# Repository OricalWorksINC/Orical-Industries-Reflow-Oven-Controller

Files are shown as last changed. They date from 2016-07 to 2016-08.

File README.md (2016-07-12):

Reflow Oven Controller
====================
Big Thanks to Ed Simmons <ed@estechnical.co.uk> , Karl Pitrich <karl@pitrich.com>
For all there hard work on the original code that this is based on.

**News**
New method of prosscesing for better performance!
Adding Serial for co-processor to process the steppers and other calculations and operations

 NEW HARDWARE COMING SOON AND FIRMWARE REVISIONS FOR TUNNLE OVENS!

**Arduino-based reflow oven controller with:**
* [PID] loop control
* [Wave Packet] and [Phase Fired] control for AC outputs
* graphic TFT LC-Display, drawing the temperature curves
  * using an [Adafruit 1.8" TFT] or derivate display
* solely controlled using a cheap rotary encoder and its single button
* stores up to 30 temperature profiles in EEPROM
* configurable PID-parameters
* simple, small hardware to drive loads up to 600V and up to 8A
* hardware can
  * measure two temperatures independently
  * drive two AC loads, such as heater and fan
* could also be used for slow coockers
* *Please Note*: Requires Arduino IDE 1.5.x or newer

(c) 2016 John Reichard <john@hobbywizards.com>
in part based on a project (c) 2013 Ed Simmons <ed@estechnical.co.uk> , (c) 2014 Karl Pitrich <karl@pitrich.com>

**Post action shot**

CycleWithOverflow | Warning
------------ | -------------

## Warning: This project operates with possibly lethal mains voltage. If you are unsure what to do, don't do it and get help from an experienced tinkerer with professional training.

**Completed build**

Completed1 | Completed2
------------ | -------------

Introduction
====================

This Reflow Oven Controller relies on an [Arduino Pro Micro], which is similar to the Leonardo and easily obtainable on eb*y for less than $10, plus my custom shield, which is actually more like a motherboard.

As I believe it is not wise to have a mess of wiring and tiny breakout-boards for operating mains powered equipment, I've decided to design custom board with easily obtainable components.

The hardware can be found in the [folder hardware], including the Eagle schematics and PCB layout files. It should fit the freemium version of Eagle. Here are preview images:

PCB
Schematic

From my manufacturing run, I have some spare PCBs and parts. They are available at my [tindie store].

The board contains the [Arduino Pro Micro], very simple [Zero crossing] detection circuit, used to align control logic to mains frequency, two [MAX31855] thermocouple-to-digital converters and two [Sharp S202S01] PCB-mount solid state relays, mounted on cheap [Fischer SK409 50,8] heat sinks. The current software uses only one of the thermocouples, so you need to populate one IC only. If you're lucky, you can get free samples of the MAX31855 from Maxim.

The software uses [PID] control of the heater and fan output for improved temperature stability. The heater AC load is controlled using [Wave Packet] control in order to minimize RF interference and load on the relay. For the fan motor, [Phase Fired] control has been implemented.

Please note that all important timings are *based on the mains frequency*, so the circuit will **not work** properly without mains connection.

But for testing, I've added an additional timer to simulate the zero-crossings, in order to run the software without being connected to mains. The software should work in 50 and 60Hz mains, the 60Hz version is not tested, though.

Errata and construction infos
========

Issue | Notes
------------ | -------------

Code can only be uploded with the Arduino 1.0.6 IDE or the LCD won't dysplay anything in my case.

Screenshots and usage information
========

Image | Information
------------ | -------------
CycleWithOverflow | *Display after a cylcle has been completed. The blue line is the setpoint, the red line the actual temperature measured by the thermocouple. Note that the graph wraps around automatically. 'Sp' is the current setpoint calculated by the PID loop. In the lower line there are: Current heater and fan outputs, both in percent, and the current temperature rise or drop rate in °C per second. The graph will draw orientation lines every 50°C up to the peak temperature set in the selected profile.*
MenuDefault | *The main menu can be navigated by rotating the encoder (sic!). Clicking enters the menu item, or navigates to the submenu. Doubleclick moves up or back or exits the menu item.*
FanSpeedEdit | *To edit a setting, click once to enter edit mode (red cursor), then rotate to change the value, click again to save. Doubleclick will exit without saving.*
MenuEditProfile | -
ProfileSettings | *Typical solder profile settings...*
ProfileSettingsEdit | *These parameters can be easily edited using the encoder as described above.*
MenuLoadProfile | *Up to 30 Profiles can be loaded and saved. You have to do this manually, so that you can have 'save-as' functionality without overwriting existing profiles.*
PIDValues | *Current pid values for my 1300W 20$ toaster oven.*
PIDValuesEdit | *Editing is simple, like above. Note that, unlike with the profile settings, the PID values will be automatically stored to EEPROM when you exit the submenu by doubleclicking.*

Obtaining the source code
====================

Get the code using `git`.

	git clone https://github.com/OricalWorksINC/reflowOvenController

or [download a Snapshot].

I've added some libraries I've used as submodules to the git repositroy, so it is important that, after cloning this repository, you do 

    git submodule update --init

to fetch all involved libraries. (See: [Submodule Cheat Sheet])

Installation
====================

Of course, you need to have the Arduino IDE installed. I've worked with version 1.5.x only and I will not support older versions. Get it from the [Arduino Download] page or upgrade you current Arduino setup.

There as several dependencies you need to install. 

If you are unfamiliar with Arduino Libraries, please read [the library guide].
Basically, each library needs to be liked or copied into your Arduino library folder.

On a Mac, this is how you link the submodule libraries to your Arduino libraries folder:

    cd ~/Documents/Arduino/Libraries
    ln -s ~/Development/<reflow source code>/libraries
    
My code uses [TimerOne] for basic timing, for the 1.8" TFT I've used [Adafruit_ST7735], which requires [Adafruit_GFX]. I **strongly suggest** to use my **modified version** of [Adafruit_ST7735-pit], as it **performs much better**, but requires you to use SPI, which my board does anyway.

For the user interface you require my own [Menu] and [ClickEncoder] libraries, which are included as submodules.

All other libraries need to be downloaded and installed.

After you've installed all libraries, open the Arduino IDE, open the ReflowController.pde sketch (using File->Open).

Select the right hardware from the Tools->Board menu. (Use Leonardo for the Pro Micro)

Compile the firmware (Sketch->Verify) to test everything is installed correctly. If something's wrong, feel free to post an issue here on github, I will look into it.

Now, choose the correct serial port from Tools->Serial Port and then upload the code.
*Remember* that a standard compile will get stuck at "Calibrating..." without proper mains connection, so that zero crossing interrupts can occur.

I could not fit PID Autotuning into the limited space of the Arduino in addition the normal code. So if you want to try to autotune you PID Loop, install the [PID_AutoTune] Library, `#define PIDTUNE 1` in the .ino file, then recompile and download do the Arduino.

As all timing relies on Zero Crossing detection, you need to `#define FAKE_HW 1` and install [TimerThree] when you want to run without actual hardware *and/or* without mains connection.

Things to note
====================

* The [MAX31855] does not like the thermocouple being grounded; It must be isolated from ground or earth.
* The PID Loop must be tuned individually for each oven. It will *not* work out of the box. 
* [PID Autotune] is not very useful, as it seems to be able to tune only to keep a specific temperature value, which is not what we do in a reflow oven. Also, at least my oven seems to be very non-linear when heating up.
* When rewiring inside your oven, use only wiring that can withstand high temperatures. I use silicone coated lace.
* Do not solder wiring inside you oven, the temperature might desolder you joints. **Crimp everything.**
* Use proper earth ground connection for your ovens chassis.
* 

 ******** How To Upgrade Arduino For Faster Speeds! *********
 
 To boost your Arduino Uno's performance up to 25% faster, all you have to do is replace the 16 MHz crystal with 20 MHz crystal, and update the bootloader with one that designed for this upgraded speed (see instruction below).
 
 Please note that this is NOT overclocking, we'll just tuning it to maximum speed allowed by manufacturer as stated in ATmega328 datasheet. So it's 100% safe and guaranteed to run as reliable as before, it's just 25% faster :) up to nearly 20 MIPS!
Step 1: Add following content to your boards.txt (located in hardware/arduino sub-directory of the Arduino application directory, i.e. \Program Files (x86)\Arduino\hardware\arduino in default installation path on 64-bit Windows (or \Program Files\Arduino\hardware\arduino if you're still using the immortal WinXP ;)...

##############################################################

atmega328_20.name=Arduino Uno++ 20MHz

atmega328_20.upload.protocol=stk500
atmega328_20.upload.maximum_size=30720
atmega328_20.upload.speed=57600

atmega328_20.bootloader.low_fuses=0xFF
atmega328_20.bootloader.high_fuses=0xDA
atmega328_20.bootloader.extended_fuses=0x05
atmega328_20.bootloader.path=atmega
atmega328_20.bootloader.file=ATmega328_20MHz.hex
atmega328_20.bootloader.unlock_bits=0x3F
atmega328_20.bootloader.lock_bits=0x0F

atmega328_20.build.mcu=atmega328p
atmega328_20.build.f_cpu=20000000L
atmega328_20.build.core=arduino

----------------- End Of Code ----------------

Step 2: Create new file with name ATmega328_20MHz.hex under hardware/arduino/bootloaders/atmega sub-directory with following content:

------------- Start Of Code --------------

:107800000C94343C0C94513C0C94513C0C94513CE1
:107810000C94513C0C94513C0C94513C0C94513CB4
:107820000C94513C0C94513C0C94513C0C94513CA4
:107830000C94513C0C94513C0C94513C0C94513C94
:107840000C94513C0C94513C0C94513C0C94513C84
:107850000C94513C0C94513C0C94513C0C94513C74
:107860000C94513C0C94513C11241FBECFEFD8E036
:10787000DEBFCDBF11E0A0E0B1E0ECE8FFE702C061
:1078800005900D92A230B107D9F712E0A2E0B1E065
:1078900001C01D92AD30B107E1F70E94313D0C945B
:1078A000C43F0C94003C982F92959F709A30B8F08A
:1078B000292F295A8F708A3078F0982F995A809101
:1078C000C00085FFFCCF2093C6008091C00085FFDB
:1078D000FCCF9093C6000895982F905DF0CF292F8C
:1078E000205DE8CF982F8091C00085FFFCCF90935A
:1078F000C6000895EF92FF920F931F93EE24FF248A
:1079000087018091C00087FD17C00894E11CF11C1D
:10791000011D111D81EDE81682E1F80683E10807DB
:1079200080E0180770F3E0910401F09105010995DA
:107930008091C00087FFE9CF8091C6001F910F9111
:10794000FF90EF9008950E947A3C982F8091C0009C
:1079500085FFFCCF9093C600913628F4903308F051
:107960009053892F08959755892F08951F930E944A
:10797000A33C182F0E94A33C1295107F810F1F91EA
:1079800008951F93182F882321F00E947A3C1150EC
:10799000E1F71F9108951F93182F0E947A3C8032BF
:1079A00049F0809103018F5F809303018530C1F01E
:1079B0001F9108958091C00085FFFCCF84E18093E2
:1079C000C6008091C00085FFFCCF1093C600809157
:1079D000C00085FFFCCF80E18093C6001F91089511
:1079E000E0910401F091050109951F9108950E940D
:1079F0007A3C803241F0809103018F5F80930301D4
:107A0000853081F008958091C00085FFFCCF84E12E
:107A10008093C6008091C00085FFFCCF80E18093F9
:107A2000C6000895E0910401F091050109950895BB
:107A300044EF51E08823A1F02D9A28EE33E0FA01BB
:107A40003197F1F721503040D1F72D9828EE33E0EF
:107A5000FA013197F1F721503040D1F7815061F7A9
:107A600008953F924F925F926F927F928F929F9272
:107A7000AF92BF92CF92DF92EF92FF920F931F933C
:107A8000CF93DF93000084E18093C4001092C5007F
:107A900088E18093C10086E08093C2005098589A94
:107AA000259A81E00E94183D24E1F22E9EE1E92E04
:107AB00085E9D82E0FE0C02E10E1B12EAA24A394A0
:107AC000B1E49B2EA6E58A2EF2E57F2EE0E26E2E33
:107AD00079E4572E63E5462E50E5352E0E947A3C18
:107AE0008033B1F18133B9F1803409F46FC081344E
:107AF00009F476C0823409F485C0853409F488C05D
:107B0000803531F1823521F1813511F1853509F466
:107B100085C0863509F48DC0843609F496C0843753
:107B200009F403C1853709F472C1863709F466C0C8
:107B3000809103018F5F80930301853079F6E09196
:107B40000401F091050109950E947A3C803351F6B9
:107B50000E94F73CC3CF0E947A3C803249F7809163
:107B6000C00085FFFCCFF092C6008091C00085FF69
:107B7000FCCF9092C6008091C00085FFFCCF809220
:107B8000C6008091C00085FFFCCF7092C600809136
:107B9000C00085FFFCCF6092C6008091C00085FFC9
:107BA000FCCF5092C6008091C00085FFFCCF409270
:107BB000C6008091C00085FFFCCF3092C600809146
:107BC000C00085FFFCCFB092C60088CF0E947A3CEF
:107BD000863808F4BDCF0E947A3C0E94F73C7ECFE5
:107BE0000E947A3C803809F49CC0813809F40BC1AA
:107BF000823809F430C1883909F48FC080E00E94CE
:107C0000CB3C6CCF84E10E94C13C0E94F73C66CF24
:107C100085E00E94C13C0E94F73C60CF0E947A3C04
:107C2000809306010E947A3C809307010E94F73CF2
:107C300055CF0E947A3C803309F411C183E00E9441
:107C4000C13C80E00E94CB3C49CF0E947A3C8093AB
:107C500009020E947A3C8093080280910C028E7F78
:107C600080930C020E947A3C853409F409C180910A
:107C7000080290910902892B89F000E010E00E942F
:107C80007A3CF801E85FFE4F80830F5F1F4F8091C1
:107C90000802909109020817190788F30E947A3C9C
:107CA000803209F045CF80910C0280FFF5C06091D1
:107CB000060170910701660F771F709307016093AB
:107CC0000601A0910802B09109021097C9F0E8E0FE
:107CD000F1E09B01AD014E0F5F1FF999FECF32BD60
:107CE00021BD819180BDFA9AF99A2F5F3F4FE41729
:107CF000F50799F76A0F7B1F7093070160930601E0
:107D00008091C00085FFFCCFF092C6008091C0003A
:107D100085FFFCCFB092C600E1CE83E00E94CB3C51
:107D2000DDCE82E00E94CB3CD9CE0E947A3C80938B
:107D300009020E947A3C809308028091060190918A
:107D40000701880F991F90930701809306010E94F5
:107D50007A3C853409F49AC080910C028E7F80931E
:107D60000C020E947A3C803209F0B8CE8091C000AB
:107D700085FFFCCFF092C600A0910802B0910902E5
:107D80001097C1F180910C02082F0170182F1695E1
:107D90001170E0910601F0910701AF014F5F5F4F55
:107DA000BA0120E030E00023B1F4112339F49491BA
:107DB0008091C00085FFFCCF9093C6002F5F3F4F9E
:107DC000CB010196FA012A173B0780F4BC014F5FF3
:107DD0005F4F002351F3F999FECFF2BDE1BDF89A50
:107DE00090B58091C00085FFFCCFE6CF709307016E
:107DF000609306018091C00085FDE5CE8091C000B2
:107E000085FFF8CFE0CE81E00E94CB3C67CE0E9498
:107E10007A3C803209F08CCE8091C00085FFFCCF87
:107E2000F092C6008091C00085FFFCCFE092C600B2
:107E30008091C00085FFFCCFD092C6008091C00029
:107E400085FFFCCFC092C6008091C00085FFFCCFAB
:107E5000B092C60043CE80E10E94CB3C3FCE0E9450
:107E60007A3C0E947A3C182F0E947A3C112309F434
:107E700083C0113009F484C08FE00E94CB3C2ECE29
:107E800080910C02816080930C02F1CE80910C02F3
:107E9000816080930C0265CF809107018823880F51
:107EA000880B8A2180930B02809106019091070133
:107EB000880F991F90930701809306018091080213
:107EC00080FF09C080910802909109020196909369
:107ED000090280930802F894F999FECF1127E091E6
:107EE0000601F0910701C8E0D1E08091080290916D
:107EF0000902103091F40091570001700130D9F35C
:107F000003E000935700E89500915700017001309D
:107F1000D9F301E100935700E89509901990009179
:107F2000570001700130D9F301E000935700E89544
:107F30001395103498F0112700915700017001300B
:107F4000D9F305E000935700E895009157000170C0
:107F50000130D9F301E100935700E895329602977A
:107F600009F0C7CF103011F00296E5CF11248091AF
:107F7000C00085FFC5CEC8CE8EE10E94CB3CAECD01
:0C7F800085E90E94CB3CAACDF894FFCF0D
:027F8C00800073
:040000030000780081
:00000001FF

--------- End of Code ---------

Step 3: desolder the old 16 Mhz crystal from Arduino Uno board. Please note that this action may void your warranty, please proceed on your own risk! If you're unsure with this, perhaps it's better to build a brand new Arduino compatible board by your own from scratch. For example, you can buy Playduino-One kit from Play-Zone — they ship worldwide — for Fr. 19.9 (about USD 21). If you live in Indonesia, you can also purchase Playduino-One Kit from azTech for only Rp150.000,- (less than USD 14).
Step 4: Install a 20 MHz crystal. Soldering should be easy since space on bottom surface is sparse.
Step 5: Burn the bootloader: open Arduino IDE, if you've done step #1 correctly then a new board should be appear under Tools > Board menu with name Arduino Uno++ 20MHz. Select the new board, attach USB cable to Arduino (or ISP programmer if you build Playduino One), and execute Tools > Burn Bootloader command. That's all, now you have a much faster Arduino!

Licensing
====================
```
The MIT License (MIT)

Copyright (c) 2016 JohnReichard
All rights reserved.

Permission is hereby granted, free of charge, to any person obtaining a copy
of this software and associated documentation files (the "Software"), to deal
in the Software without restriction, including without limitation the rights
to use, copy, modify, merge, publish, distribute, sublicense, and/or sell
copies of the Software, and to permit persons to whom the Software is
furnished to do so, subject to the following conditions:

The above copyright notice and this permission notice shall be included in
all copies or substantial portions of the Software.

THE SOFTWARE IS PROVIDED "AS IS", WITHOUT WARRANTY OF ANY KIND, EXPRESS OR
IMPLIED, INCLUDING BUT NOT LIMITED TO THE WARRANTIES OF MERCHANTABILITY,
FITNESS FOR A PARTICULAR PURPOSE AND NONINFRINGEMENT. IN NO EVENT SHALL THE
AUTHORS OR COPYRIGHT HOLDERS BE LIABLE FOR ANY CLAIM, DAMAGES OR OTHER
LIABILITY, WHETHER IN AN ACTION OF CONTRACT, TORT OR OTHERWISE, ARISING FROM,
OUT OF OR IN CONNECTION WITH THE SOFTWARE OR THE USE OR OTHER DEALINGS IN
THE SOFTWARE.
```

[PID Autotune]:https://github.com/br3ttb/Arduino-PID-AutoTune-Library
[Submodule Cheat Sheet]:http://blog.jacius.info/git-submodule-cheat-sheet/
[ESTechnical]:http://www.estechnical.co.uk
[Arduino Download]:http://arduino.cc/en/Main/Software
[folder hardware]:https://github.com/0xPIT/reflowOvenController/tree/master/hardware
[download a Snapshot]:https://github.com/0xPIT/reflowOvenController/archive/master.zip
[the library guide]:http://arduino.cc/en/Guide/Libraries
[PID]:http://en.wikipedia.org/wiki/PID_controller
[Wave Packet]:http://de.wikipedia.org/wiki/Schwingungspaketsteuerung
[Phase Fired]:http://en.wikipedia.org/wiki/Phase-fired_controllers 
[Adafruit 1.8" TFT]:http://www.adafruit.com/products/358
[MAX31855]:http://www.maximintegrated.com/en/products/analog/sensors-and-sensor-interface/MAX31855.html
[Fischer SK409 50,8]:http://www.pollin.de/shop/dt/NzE5OTY1OTk-
[Sharp S202S01]:http://sharp-world.com/products/device/lineup/data/pdf/datasheet/s102s01_e.pdf
[Zero crossing]:http://en.wikipedia.org/wiki/Zero_crossing
[TimerOne]:http://playground.arduino.cc/Code/Timer1
[TimerThree]:http://playground.arduino.cc/Code/Timer1
[Adafruit_ST7735]:https://github.com/adafruit/Adafruit-ST7735-Library
[Adafruit_GFX]:https://github.com/adafruit/Adafruit-GFX-Library
[Adafruit_ST7735-pit]:https://github.com/0xPIT/Adafruit-ST7735-Library
[Menu]:https://github.com/0xPIT/menu
[ClickEncoder]:https://github.com/0xPIT/encoder
[Arduino Pro Micro]:https://www.sparkfun.com/products/12640
[tindie store]:https://www.tindie.com/products/0xPIT/reflow-oven-controller-motherboard-for-arduino-pro-micro/

[CycleWithOverflow]:https://raw.githubusercontent.com/0xPIT/reflowOvenController/master/images/CycleWithOverflow.jpg
[FanSpeedEdit]:https://raw.githubusercontent.com/0xPIT/reflowOvenController/master/images/FanSpeedEdit.jpg
[MenuDefault]:https://raw.githubusercontent.com/0xPIT/reflowOvenController/master/images/Menu.jpg
[MenuLoadProfile]:https://raw.githubusercontent.com/0xPIT/reflowOvenController/master/images/MenuLoadProfile.jpg
[MenuEditProfile]:https://raw.githubusercontent.com/0xPIT/reflowOvenController/master/images/MenuEditProfile.jpg
[PIDValuesEdit]:https://raw.githubusercontent.com/0xPIT/reflowOvenController/master/images/PIDValuesEdit.jpg
[ProfileSettings]:https://raw.githubusercontent.com/0xPIT/reflowOvenController/master/images/ProfileSettings.jpg
[PIDValues]:https://raw.githubusercontent.com/0xPIT/reflowOvenController/master/images/PIDValues.jpg
[ProfileSettingsEdit]:https://raw.githubusercontent.com/0xPIT/reflowOvenController/master/images/ProfileSettingsEdit.jpg

[Warning]:http://www.proshieldsafetysigns.co.uk/signs/59793_signs.jpg
[ImgPCB]:https://raw.githubusercontent.com/0xPIT/reflowOvenController/master/hardware/v0.2.brd.preview.png
[ImgSCH]:https://raw.githubusercontent.com/0xPIT/reflowOvenController/master/hardware/v0.2.sch.preview.png

[ImgMissingTrace]:https://raw.githubusercontent.com/0xPIT/reflowOvenController/master/images/MissingTrace.jpg
[Completed1]:https://raw.githubusercontent.com/0xPIT/reflowOvenController/master/images/Completed1.jpg
[Completed2]:https://raw.githubusercontent.com/0xPIT/reflowOvenController/master/images/Completed2.jpg

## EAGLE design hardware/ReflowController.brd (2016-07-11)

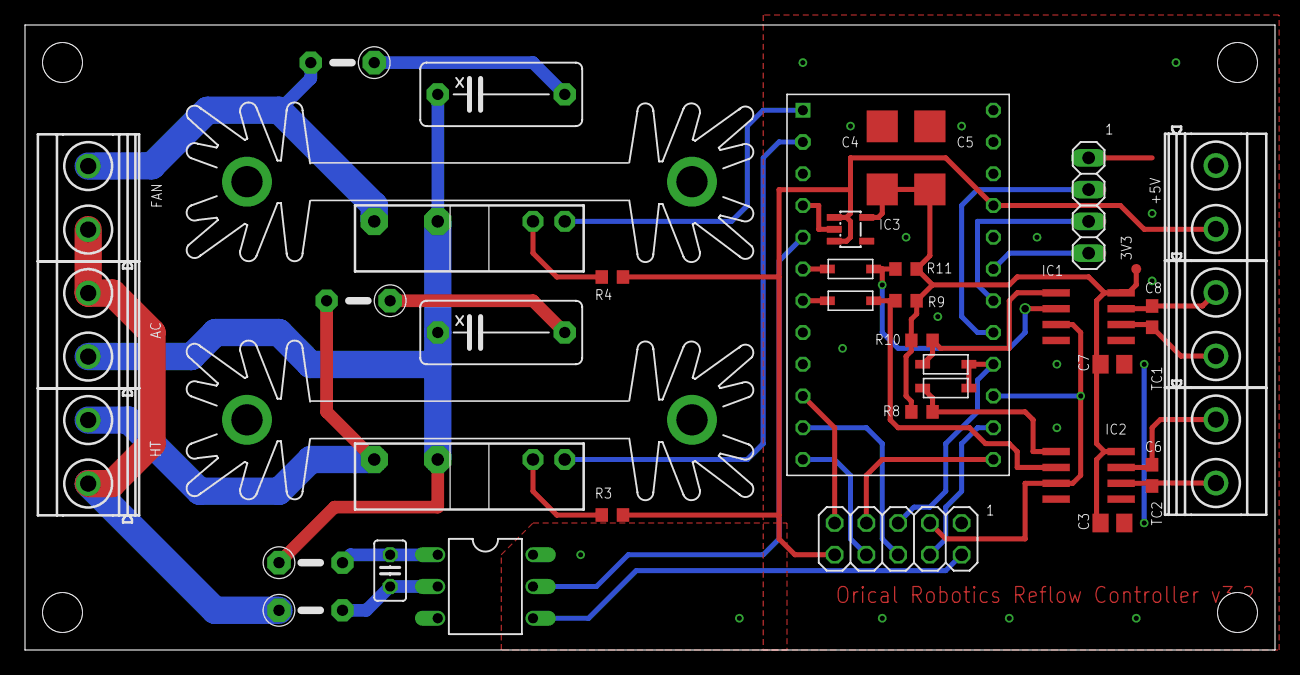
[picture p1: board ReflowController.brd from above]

Board: 2 copper layers, 100.0 x 50.0 mm, 41 parts (0 on the bottom side), 36 nets.

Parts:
3V3: TPTP08R; TP08R
A1: ARDUINO_PRO_NANO
AC: MKDSN1,5/2-5,08
C1, C2: 100n; XC10B5
C3, C7: 100n; C0805
C4, C5: 10µ; C/6032-28R
C6, C8: 10n; C0603
C9: 100n; C025-025X050
D1, D2, D3, D4: SOD-123
ENC: 1X04
FAN: MKDSN1,5/2-5,08
HT: MKDSN1,5/2-5,08
IC1, IC2: MAX31855; SOIC8
IC3: LP298XS; SOT23-5L
K1, K2: S202S01; S102S01
KK1, KK2: SK104-PAD
LCD: 2X05
OC1: H11A1M; DIL06
R1, R2: 100R; 0207/5V
R3, R4: 120R; R0603
R5, R6: 47k; 0207/5V
R8, R9, R10, R11: 10k; R0603
TC1, TC2: MKDSN1,5/2-5,08
VCC: MKDSN1,5/2-5,08

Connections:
+3V3: 3V3.TP, C3.1, C4.+, C5.+, C7.1, IC1.4, IC2.4, IC3.5, R8.2, R9.2, R10.2, R11.2
AC1: AC.1, C1.1, C2.1, K1.2, K2.2, R5.1
AC2: AC.2, FAN.1, HT.1, R6.1
AC_OUT1: HT.2, K1.1, R1.2
AC_OUT2: FAN.2, K2.1, R2.2
GND: A1.P$3, A1.P$4, A1.P$23, C3.2, C4.-, C5.-, C7.2, ENC.1, IC1.1, IC2.1, IC3.2, LCD.1, LCD.2, OC1.4, VCC.1
LCD_CS: A1.P$13, LCD.7
LCD_DC: A1.P$12, LCD.8
LCD_RESET: A1.P$11, LCD.6
MISO: A1.P$15, IC1.7, IC2.7, LCD.3
MOSI: A1.P$14, LCD.4
unnamed: C8.2, IC1.2, TC1.2
unnamed: C6.2, IC2.2, TC2.2
unnamed: C6.1, IC2.3, TC2.1
unnamed: A1.P$17, ENC.2
unnamed: A1.P$18, ENC.3
unnamed: C1.2, R1.1
unnamed: C2.2, R2.1
unnamed: A1.P$19, ENC.4
unnamed: C9.1, OC1.1, R5.2
unnamed: C9.2, OC1.2, R6.2
unnamed: C8.1, IC1.3, TC1.1
unnamed: K1.3, R3.2
unnamed: K2.3, R4.2
unnamed: D2.A, IC2.6, R9.1
unnamed: D1.A, IC2.5, R8.1
unnamed: D4.A, IC1.6, R11.1
unnamed: D3.A, IC1.5, R10.1
SCK: A1.P$16, D1.C, D3.C, LCD.5
SD_CS: A1.P$10, LCD.9
SSR1: A1.P$2, K1.4
SSR2: A1.P$1, K2.4
TC1_CS: A1.P$6, D4.C
TC2_CS: A1.P$7, D2.C
VCC: A1.P$21, IC3.1, IC3.3, LCD.10, R3.1, R4.1, VCC.2
ZEROX: A1.P$5, OC1.5

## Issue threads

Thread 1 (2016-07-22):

IDE Version? Confusion..

mrred2k, 2016-07-22:
The Readme is specifing 2 different Arduino IDE Versions to be used. The older says 1.5*+ and the newer code says use 1.0* ..

What is correct?

OricalWorksINC, 2016-07-24:
Hello mrred2k
I've had issues with the newer IDE and the LCD not working and then be fine
when I switch back, but thats just me.
experiment and if u find any issues or anything that needs to be updated
just request a push on github with the updated files and I will take a look.
Thx so much & I hope this helps.
John P. Reichard

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

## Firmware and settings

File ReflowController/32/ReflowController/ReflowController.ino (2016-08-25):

//  !!!!!!! FOR 32-BIT INTEl CURRY BASED BOARDS !!!!!!!

// ----------------------------------------------------------------------------
// Orical Robobtics Reflow Oven Controller Fork THX to Origonal Devs on wiki
// New Developers below
// John Reichard
// ----------------------------------------------------------------------------
// Adding Serial for co-processor to process the steppers and other calculations and operations
//
//#define FAKE_HW 1
//#define PIDTUNE 1 // autotune wouldn't fit in the 28k available on the arduino pro micro.
// -------NEW HARDWARE COMING SOON!!!-------
// run a calibration loop that measures how many timer ticks occur between 2 zero corssings
// FIXME: does not work reliably at the moment, so a oscilloscope-determined value is used.
//#define WITH_CALIBRATION 1 // loop timing calibration
#define DEFAULT_LOOP_DELAY 89 // should be about 16% less for 60Hz mains

#include <Wire.h>
#include <CurieEEPROM.h>
#include <EEPROM.h>
#include <PID_v1.h>
#include <Adafruit_GFX.h>
#include <Adafruit_ST7735.h>
#include <SPI.h>
#include <Menu.h>
#include <TimerOne.h>
#include <ClickEncoder.h>
#include "temperature.h"
#include "helpers.h"
#ifdef FAKE_HW
#include <TimerThree.h>
#endif
#ifdef PIDTUNE
#include <PID_AutoTune_v0.h>
#endif
byte x = 0;
// ----------------------------------------------------------------------------

const char * ver = "3.2";

// ----------------------------------------------------------------------------

//#define MS_PER_SINE 100       // for 50Hz mains; 100ms per sinusoid
#define MS_PER_SINE  83.333 // for 60Hz Mains; 83,3333ms per sinusoid

// ----------------------------------------------------------------------------
// Hardware Configuration 

// 1.8" TFT via SPI -> breadboard
#ifdef FAKE_HW
#define LCD_CS  10
#define LCD_DC   7
#define LCD_RST  8
#else 
#define LCD_CS   10
#define LCD_DC   9
#define LCD_RST  8
#endif

// Thermocouple via SPI
#define THERMOCOUPLE1_CS  3

#define PIN_HEATER   0 // SSR for the heater
#define PIN_FAN      1 // SSR for the fan

#define PIN_ZX       2 // pin for zero crossing detector
#define INT_ZX       1 // interrupt for zero crossing detector
// Leonardo == Pro Micro:
//   Pin: 3 2 0 1 7
//   Int: 0 1 2 3 4 

// ----------------------------------------------------------------------------

#define WITH_SPLASH 1

// ----------------------------------------------------------------------------

volatile uint32_t timerTicks     = 0;
volatile uint32_t zeroCrossTicks = 0;
volatile uint8_t  phaseCounter   = 0;

char buf[20]; // generic char buffer

// ----------------------------------------------------------------------------

// data type for the values used in the reflow profile
typedef struct profileValues_s {
  int16_t soakTemp;
  int16_t soakDuration;
  int16_t peakTemp;
  int16_t peakDuration;
  double  rampUpRate;
  double  rampDownRate;
  uint8_t checksum;
} 
Profile_t;

Profile_t activeProfile; // the one and only instance
int activeProfileId = 0;

int idleTemp = 50; // the temperature at which to consider the oven safe to leave to cool naturally
int fanAssistSpeed = 33; // default fan speed

const uint8_t maxProfiles = 30;

// EEPROM offsets
const uint16_t offsetFanSpeed   = maxProfiles * sizeof(Profile_t) + 1; // one byte
const uint16_t offsetProfileNum = maxProfiles * sizeof(Profile_t) + 2; // one byte
const uint16_t offsetPidConfig  = maxProfiles * sizeof(Profile_t) + 3; // sizeof(PID_t)

Thermocouple A;

// ----------------------------------------------------------------------------

uint32_t startCycleZeroCrossTicks;
uint32_t lastUpdate = 0;
uint32_t lastDisplayUpdate = 0;

// ----------------------------------------------------------------------------
// UI

// NB: Adafruit GFX ASCII-Table is bogous: https://github.com/adafruit/Adafruit-GFX-Library/issues/22
//
Adafruit_ST7735 tft = Adafruit_ST7735(LCD_CS, LCD_DC, LCD_RST);

#ifdef FAKE_HW
ClickEncoder Encoder(A0, A1, A2, 2);
#else
ClickEncoder Encoder(A1, A0, A2, 2);
#endif

Menu::Engine Engine;

int16_t encMovement;
int16_t encAbsolute;
int16_t encLastAbsolute = -1;

const uint8_t menuItemsVisible = 6;
const uint8_t menuItemHeight = 12;
bool menuUpdateRequest = true;
bool initialProcessDisplay = false;

// ----------------------------------------------------------------------------
// state machine

typedef enum {
  None     = 0,
  Idle     = 1,
  Settings = 2,
  Edit     = 3,

  UIMenuEnd = 9,

  RampToSoak = 10,
  Soak,
  RampUp,
  Peak,
  RampDown,
  CoolDown,

  Complete = 20,

  Tune = 30
} 
State;

State currentState  = Idle;
State previousState = Idle;
bool stateChanged = false;
uint32_t stateChangedTicks = 0;

// ----------------------------------------------------------------------------

// track menu item state to improve render preformance
typedef struct {
  const Menu::Item_t *mi;
  uint8_t pos;
  bool current;
} 
LastItemState_t;

LastItemState_t currentlyRenderedItems[menuItemsVisible];

void clearLastMenuItemRenderState() {
  // memset(&currentlyRenderedItems, 0xff, sizeof(LastItemState_t) * menuItemsVisible);
  for (uint8_t i = 0; i < menuItemsVisible; i++) {
    currentlyRenderedItems[i].mi = NULL;
    currentlyRenderedItems[i].pos = 0xff;
    currentlyRenderedItems[i].current = false;
  }
}

// ----------------------------------------------------------------------------

extern const Menu::Item_t miRampUpRate, miRampDnRate, miSoakTime, 
miSoakTemp, miPeakTime, miPeakTemp,
miLoadProfile, miSaveProfile,
miPidSettingP, miPidSettingI, miPidSettingD,
miFanSettings;

// ----------------------------------------------------------------------------
// PID

uint8_t fanValue;
uint8_t heaterValue;

double Setpoint;
double Input;
double Output;

typedef struct {
  double Kp;
  double Ki;
  double Kd;
} 
PID_t;

PID_t heaterPID = { 
  4.00, 0.05,  2.00 };
PID_t fanPID    = { 
  1.00, 0.03, 10.00 };

PID PID(&Input, &Output, &Setpoint, heaterPID.Kp, heaterPID.Ki, heaterPID.Kd, DIRECT);

#ifdef PIDTUNE
PID_ATune PIDTune(&Input, &Output);

double aTuneStep       =  50,
aTuneNoise      =   1,
aTuneStartValue =  50; // is set to Output, i.e. 0-100% of Heater

unsigned int aTuneLookBack = 30;
#endif

// ----------------------------------------------------------------------------

bool menuExit(const Menu::Action_t a) {
  clearLastMenuItemRenderState();
  Engine.lastInvokedItem = &Menu::NullItem;
  menuUpdateRequest = false;
  return false;
}

// ----------------------------------------------------------------------------

bool menuDummy(const Menu::Action_t a) {
  return true;
}

// ----------------------------------------------------------------------------

void printDouble(double val, uint8_t precision = 1) {
  ftoa(buf, val, precision);
  tft.print(buf);
}

// ----------------------------------------------------------------------------

void getItemValuePointer(const Menu::Item_t *mi, double **d, int16_t **i) {
  if (mi == &miRampUpRate)  *d = &activeProfile.rampUpRate;
  if (mi == &miRampDnRate)  *d = &activeProfile.rampDownRate;
  if (mi == &miSoakTime)    *i = &activeProfile.soakDuration;
  if (mi == &miSoakTemp)    *i = &activeProfile.soakTemp;
  if (mi == &miPeakTime)    *i = &activeProfile.peakDuration;
  if (mi == &miPeakTemp)    *i = &activeProfile.peakTemp;
  if (mi == &miPidSettingP) *d = &heaterPID.Kp;
  if (mi == &miPidSettingI) *d = &heaterPID.Ki;
  if (mi == &miPidSettingD) *d = &heaterPID.Kd; 
  if (mi == &miFanSettings) *i = &fanAssistSpeed;
}

// ----------------------------------------------------------------------------

bool isPidSetting(const Menu::Item_t *mi) {
  return mi == &miPidSettingP || mi == &miPidSettingI || mi == &miPidSettingD;
}

bool isRampSetting(const Menu::Item_t *mi) {
  return mi == &miRampUpRate || mi == &miRampDnRate;
}

// ----------------------------------------------------------------------------

bool getItemValueLabel(const Menu::Item_t *mi, char *label) {
  int16_t *iValue = NULL;
  double  *dValue = NULL;
  char *p;

  getItemValuePointer(mi, &dValue, &iValue);

  if (isRampSetting(mi) || isPidSetting(mi)) {
    p = label;
    ftoa(p, *dValue, (isPidSetting(mi)) ? 2 : 1); // need greater precision with pid values
    p = label;

    if (isRampSetting(mi)) {
      while(*p != '\0') p++;
      *p++ = 0xf7; 
      *p++ = 'C'; 
      *p++ = '/'; 
      *p++ = 's';
      *p = '\0';
    }
  }
  else {
    if (mi == &miPeakTemp || mi == &miSoakTemp) {
      itostr(label, *iValue, "\367C");
    }
    if (mi == &miPeakTime || mi == &miSoakTime) {
      itostr(label, *iValue, "s");
    }
    if (mi == &miFanSettings) {
      itostr(label, *iValue, "%");
    }
  }

  return dValue || iValue;
}

// ----------------------------------------------------------------------------

bool editNumericalValue(const Menu::Action_t action) { 
  if (action == Menu::actionDisplay) {
    bool initial = currentState != Edit;
    currentState = Edit;

    if (initial) {
      tft.setTextColor(ST7735_BLACK, ST7735_WHITE);
      tft.setCursor(10, 80);
      tft.print("Edit & click to save.");
      Encoder.setAccelerationEnabled(true);
    }

    for (uint8_t i = 0; i < menuItemsVisible; i++) {
      if (currentlyRenderedItems[i].mi == Engine.currentItem) {
        uint8_t y = currentlyRenderedItems[i].pos * menuItemHeight + 2;

        if (initial) {
          tft.fillRect(69, y - 1, 60, menuItemHeight - 2, ST7735_RED);
        }

        tft.setCursor(70, y);
        break;
      }
    }

    tft.setTextColor(ST7735_WHITE, ST7735_RED);

    int16_t *iValue = NULL;
    double  *dValue = NULL;
    getItemValuePointer(Engine.currentItem, &dValue, &iValue);

    if (isRampSetting(Engine.currentItem) || isPidSetting(Engine.currentItem)) {
      double tmp;
      double factor = (isPidSetting(Engine.currentItem)) ? 100 : 10;

      if (initial) {
        tmp = *dValue;
        tmp *= factor;
        encAbsolute = (int16_t)tmp;
      }
      else {
        tmp = encAbsolute;
        tmp /= factor;
        *dValue = tmp;
      }      
    }
    else {
      if (initial) encAbsolute = *iValue;
      else *iValue = encAbsolute;
    }

    getItemValueLabel(Engine.currentItem, buf);
    tft.print(buf);
    tft.setTextColor(ST7735_BLACK, ST7735_WHITE);
  }

  if (action == Menu::actionParent || action == Menu::actionTrigger) {
    clearLastMenuItemRenderState();
    menuUpdateRequest = true;
    Engine.lastInvokedItem = &Menu::NullItem;


    if (currentState == Edit) { // leave edit mode, return to menu
      if (isPidSetting(Engine.currentItem)) {
        savePID();
      }
      else if (Engine.currentItem == &miFanSettings) {
        saveFanSpeed();
      }
      // don't autosave profile, so that one can do "save as" without overwriting the current profile

      currentState = Settings;
      Encoder.setAccelerationEnabled(false);
      return false;
    }

    return true;
  }
}

// ----------------------------------------------------------------------------

bool factoryReset(const Menu::Action_t action) {
#ifndef PIDTUNE
  if (action == Menu::actionDisplay) {
    bool initial = currentState != Edit;
    currentState = Edit;

    if (initial) { // TODO: add eyecandy: colors or icons
      tft.setTextColor(ST7735_BLACK, ST7735_WHITE);
      tft.setCursor(10, 80);
      tft.print("Click to confirm");
      tft.setCursor(10, 90);
      tft.print("Doubleclick to exit");
    }
  }

  if (action == Menu::actionTrigger) { // do it
    factoryReset();
    tft.fillScreen(ST7735_WHITE);
    Engine.navigate(Engine.getParent());
    return false;
  }

  if (action == Menu::actionParent) {
    if (currentState == Edit) { // leave edit mode only, returning to menu
      currentState = Settings;
      clearLastMenuItemRenderState();
      return false;
    }
  }
#endif // PIDTUNE
}

// ----------------------------------------------------------------------------

void saveProfile(unsigned int targetProfile, bool quiet = false);

// ----------------------------------------------------------------------------

bool saveLoadProfile(const Menu::Action_t action) {
#ifndef PIDTUNE
  bool isLoad = Engine.currentItem == &miLoadProfile;

  if (action == Menu::actionDisplay) {
    bool initial = currentState != Edit;
    currentState = Edit;

    tft.setTextColor(ST7735_BLACK, ST7735_WHITE);

    if (initial) {
      encAbsolute = activeProfileId;      
      tft.setCursor(10, 90);
      tft.print("Click to exit");
    }

    if (encAbsolute > maxProfiles) encAbsolute = maxProfiles;
    if (encAbsolute <  0) encAbsolute =  0;

    tft.setCursor(10, 80);
    tft.print("Click to ");
    tft.print((isLoad) ? "load " : "save ");
    tft.setTextColor(ST7735_WHITE, ST7735_RED);
    tft.print(encAbsolute);
  }

  if (action == Menu::actionTrigger) {
    (isLoad) ? loadProfile(encAbsolute) : saveProfile(encAbsolute);
    tft.fillScreen(ST7735_WHITE);
    Engine.navigate(Engine.getParent());
    return false;
  }

  if (action == Menu::actionParent) {    
    if (currentState == Edit) { // leave edit mode only, returning to menu
      currentState = Settings;
      clearLastMenuItemRenderState();
      return false;
    }
  }
#endif // PIDTUNE
}

// ----------------------------------------------------------------------------

void toggleAutoTune();
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
void loop(void) 
{
  // --------------------------------------------------------------------------
  // handle encoder
  //
  encMovement = Encoder.getValue();
  if (encMovement) {
    encAbsolute += encMovement;
    if (currentState == Settings) {
      Engine.navigate((encMovement > 0) ? Engine.getNext() : Engine.getPrev());
      menuUpdateRequest = true;
    }
  }

  // --------------------------------------------------------------------------
  // handle button
  //
  switch (Encoder.getButton()) {
    case ClickEncoder::Clicked:
    if (currentState == Complete) { // at end of cycle; reset at click
      menuExit(Menu::actionDisplay); // reset to initial state
      Engine.navigate(&miCycleStart);
      currentState = Settings;
      menuUpdateRequest = true;
    }
    else if (currentState < UIMenuEnd) {
      menuUpdateRequest = true;
      Engine.invoke();
    }
    else if (currentState > UIMenuEnd) {
      currentState = CoolDown;
    }
    break;

    case ClickEncoder::DoubleClicked:
    if (currentState < UIMenuEnd) {
      if (Engine.getParent() != &miExit) {
        Engine.navigate(Engine.getParent());
        menuUpdateRequest = true;
      }
    }
    break;
  }

  // --------------------------------------------------------------------------
  // update current menu item while in edit mode
  //
  if (currentState == Edit) {
    if (Engine.currentItem != &Menu::NullItem) {
      Engine.executeCallbackAction(Menu::actionDisplay);      
    }
  }

  // --------------------------------------------------------------------------
  // handle menu update
  //
  if (menuUpdateRequest) {
    menuUpdateRequest = false;
    if (currentState < UIMenuEnd && !encMovement && currentState != Edit && previousState != Edit) { // clear menu on child/parent navigation
      tft.fillScreen(ST7735_WHITE);
    }  
    Engine.render(renderMenuItem, menuItemsVisible);
  }

  // --------------------------------------------------------------------------
  // track state changes
  //
  if (currentState != previousState) {
    stateChangedTicks = zeroCrossTicks;
    stateChanged = true;
    previousState = currentState;
  }

  // --------------------------------------------------------------------------

  if (zeroCrossTicks - lastUpdate >= 10) {
    uint32_t deltaT = zeroCrossTicks - lastUpdate;
    lastUpdate = zeroCrossTicks;

#ifndef FAKE_HW
    readThermocouple(&A); // should be sufficient to read it every 250ms or 500ms
#else
    A.temperature = encAbsolute;
#endif

    if (A.stat > 0) {
      thermocoupleErrorCount++;
    }
    else {
      thermocoupleErrorCount = 0;
    }

    if (thermocoupleErrorCount > TC_ERROR_TOLERANCE) {
      abortWithError(A.stat);
    }

#if 0 // verbose thermocouple error bits
    tft.setCursor(10, 40);
    for (uint8_t mask = B111; mask; mask >>= 1) {
      tft.print(mask & A.stat ? '1' : '0');
    }
#endif

    // rolling average of the temp T1 and T2
    totalT1 -= readingsT1[index];       // subtract the last reading
    readingsT1[index] = A.temperature;
    totalT1 += readingsT1[index];       // add the reading to the total
    index = (index + 1) % NUMREADINGS;  // next position
    averageT1 = totalT1 / NUMREADINGS;  // calculate the average temp

    // need to keep track of a few past readings in order to work out rate of rise
    for (int i = 1; i < NUMREADINGS; i++) { // iterate over all previous entries, moving them backwards one index
      airTemp[i - 1].temp = airTemp[i].temp;
      airTemp[i - 1].ticks = airTemp[i].ticks;     
    }

    airTemp[NUMREADINGS - 1].temp = averageT1; // update the last index with the newest average
    airTemp[NUMREADINGS - 1].ticks = deltaT;

    // calculate rate of temperature change
    uint32_t collectTicks;
    for (int i = 0; i < NUMREADINGS; i++) {
      collectTicks += airTemp[i].ticks;
    }
    rampRate = (airTemp[NUMREADINGS - 1].temp - airTemp[0].temp) / collectTicks * MS_PER_SINE;

    Input = airTemp[NUMREADINGS - 1].temp; // update the variable the PID reads

    // display update
    if (zeroCrossTicks - lastDisplayUpdate > 50) {
      lastDisplayUpdate = zeroCrossTicks;
      if (currentState > UIMenuEnd) {
        updateProcessDisplay();
      }
    }

    switch (currentState) {
#ifndef PIDTUNE
    case RampToSoak:
      if (stateChanged) {
        lastRampTicks = zeroCrossTicks;
        stateChanged = false;
        Output = 80;
        PID.SetMode(AUTOMATIC);
        PID.SetControllerDirection(DIRECT);
        PID.SetTunings(heaterPID.Kp, heaterPID.Ki, heaterPID.Kd);
        Setpoint = airTemp[NUMREADINGS - 1].temp;
      }

      updateRampSetpoint();

      if (Setpoint >= activeProfile.soakTemp - 1) {
        currentState = Soak;
      }
      break;

    case Soak:
      if (stateChanged) {
        stateChanged = false;
        Setpoint = activeProfile.soakTemp;
      }

      if (zeroCrossTicks - stateChangedTicks >= (uint32_t)activeProfile.soakDuration * MS_PER_SINE) {
        currentState = RampUp;
      }
      break;

    case RampUp:
      if (stateChanged) {
        stateChanged = false;
        lastRampTicks = zeroCrossTicks;
      }

      updateRampSetpoint();

      if (Setpoint >= activeProfile.peakTemp - 1) {
        Setpoint = activeProfile.peakTemp;
        currentState = Peak;
      }
      break;

    case Peak:
      if (stateChanged) {
        stateChanged = false;
        Setpoint = activeProfile.peakTemp;
      }

      if (zeroCrossTicks - stateChangedTicks >= (uint32_t)activeProfile.peakDuration * MS_PER_SINE) {
        currentState = RampDown;
      }
      break;

    case RampDown:
      if (stateChanged) {
        stateChanged = false;
        lastRampTicks = zeroCrossTicks;
        PID.SetControllerDirection(REVERSE);
        PID.SetTunings(fanPID.Kp, fanPID.Ki, fanPID.Kd);
        Setpoint = activeProfile.peakTemp - 15; // get it all going with a bit of a kick! v sluggish here otherwise, too hot too long
      }

      updateRampSetpoint(true);

      if (Setpoint <= idleTemp) {
        currentState = CoolDown;
      }
      break;
#endif
    case CoolDown:
      if (stateChanged) {
        stateChanged = false;
        PID.SetControllerDirection(REVERSE);
        PID.SetTunings(fanPID.Kp, fanPID.Ki, fanPID.Kd);
        Setpoint = idleTemp;
      }

      if (Input < (idleTemp + 5)) {
        currentState = Complete;
        PID.SetMode(MANUAL);
        Output = 0;
      }

#ifdef PIDTUNE
    case Tune:
      {
        Setpoint = 210.0;
        int8_t val = PIDTune.Runtime();
        PIDTune.setpoint = 210.0;

        if (val != 0) {
          currentState = CoolDown;
        }

        if (currentState != Tune) { // we're done, set the tuning parameters
          heaterPID.Kp = PIDTune.GetKp();
          heaterPID.Ki = PIDTune.GetKi();
          heaterPID.Kd = PIDTune.GetKd();

          savePID();

          tft.setCursor(40, 40);
          tft.print("Kp: "); 
          tft.print((uint32_t)(heaterPID.Kp * 100));
          tft.setCursor(40, 52);
          tft.print("Ki: "); 
          tft.print((uint32_t)(heaterPID.Ki * 100));
          tft.setCursor(40, 64);
          tft.print("Kd: "); 
          tft.print((uint32_t)(heaterPID.Kd * 100));
        }
      }
      break;
#endif
    }
  }

  // safety check that we're not doing something stupid. 
  // if the thermocouple is wired backwards, temp goes DOWN when it increases
  // during cooling, the t962a lags a long way behind, hence the hugely lenient cooling allowance.
  // both of these errors are blocking and do not exit!
  //if (Setpoint > Input + 50) abortWithError(10); // if we're 50 degree cooler than setpoint, abort
  //if (Input > Setpoint + 50) abortWithError(20); // or 50 degrees hotter, also abort

#ifndef PIDTUNE
  PID.Compute();

  // decides which control signal is fed to the output for this cycle
  if (   currentState != RampDown
    && currentState != CoolDown
    && currentState != Settings
    && currentState != Complete
    && currentState != Idle
    && currentState != Settings
    && currentState != Edit)
  {
    heaterValue = Output;
    fanValue = fanAssistSpeed;
  } 
  else {
    heaterValue = 0;
    fanValue = Output;
  }
#else
  heaterValue = Output;
  fanValue = fanAssistSpeed;
#endif

  Channels[CHANNEL_HEATER].target = heaterValue;

  double fanTmp = 90.0 / 100.0 * fanValue; // 0-100% -> 0-90° phase control
  Channels[CHANNEL_FAN].target = 90 - (uint8_t)fanTmp;
}

void memoryFeedbackScreen(uint8_t profileId, bool loading) {
  tft.fillScreen(ST7735_GREEN);
  tft.setTextColor(ST7735_BLACK);
  tft.setCursor(10, 50);
  tft.print(loading ? "Loading" : "Saving");
  tft.print(" profile ");
  tft.print(profileId);  
}
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

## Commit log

2016-07-05 Updated Libraries and Code
    Refreshing code stage
2016-07-05 Updated Code and Libraries
    [ReflowController Alternate micro.sch]
2016-07-08 Faster processing How To for Arduino
2016-07-08 Faster processing and better performance How To for Arduino
2016-07-08 Added How to for upgraded arduino
2016-07-11 Just some updates
    [ReflowController.brd]
2016-07-12 Adding Serial
    // Adding Serial for co-processor to process the steppers and other
    calculations and operations
2016-07-12 some serial updates for starting heat cycle
